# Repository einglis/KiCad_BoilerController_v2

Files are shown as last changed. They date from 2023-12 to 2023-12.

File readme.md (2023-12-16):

# Boiler Controller mk2

A whole new controller retaining the original features:

* Delayed closing valves
* Support for 24vac Nest thermostat (early US model)

And several new features:

* Multiple heating channels (zoned heating)
* ESP8266 for control and scheduling
* Greater flexibility in stat to valve mappings

The main MCU is an ESP8266 running https://github.com/einglis/SimpleNode/tree/main/examples/heating (still a WIP at the time of writing)

The valve controller is an Arduino Nano running https://github.com/einglis/boiler_valves

## HW versions

The first main board (control) had lots of drill holes that were too small; its replacement addesssed this and tidied up a few little details.

The first MCU board had pads that were too tiny to practically solder the transistors; its replacement added bigger pads, deleted the on-board status LEDs (since the MCUs have thier own), and simplified the ctrl+stat selector for the Hot Water valve.

Both replacements fixed an embarassing error where I hadn't read the ordering instructions, leaving a "Order Number Here" label present on both boards  ...along with the actual order numbers.

## v2.1 Pictures
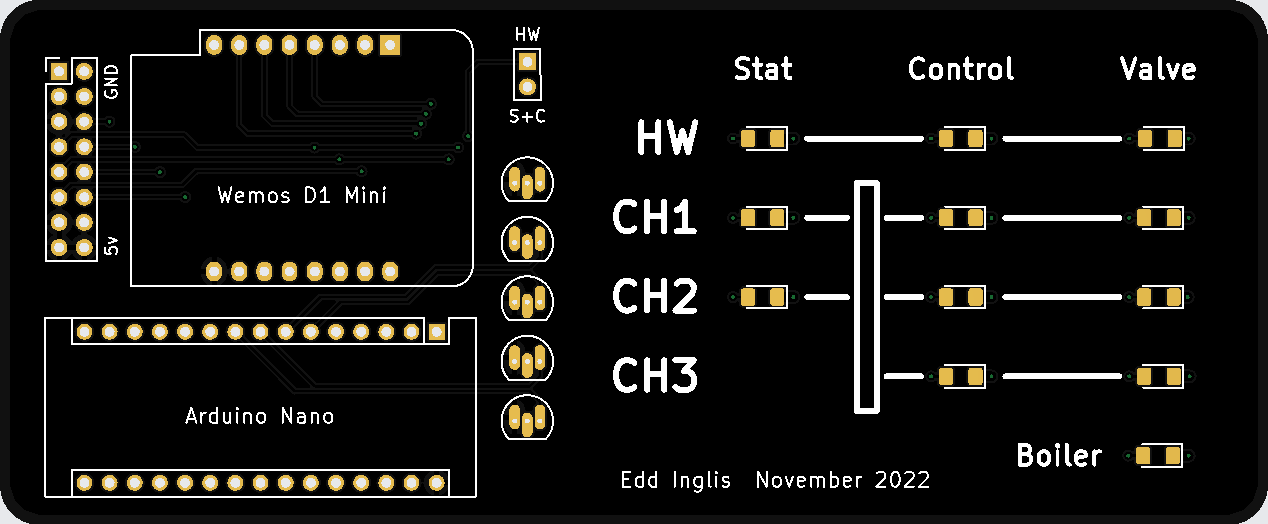
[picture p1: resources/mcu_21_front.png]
mcu_21_front

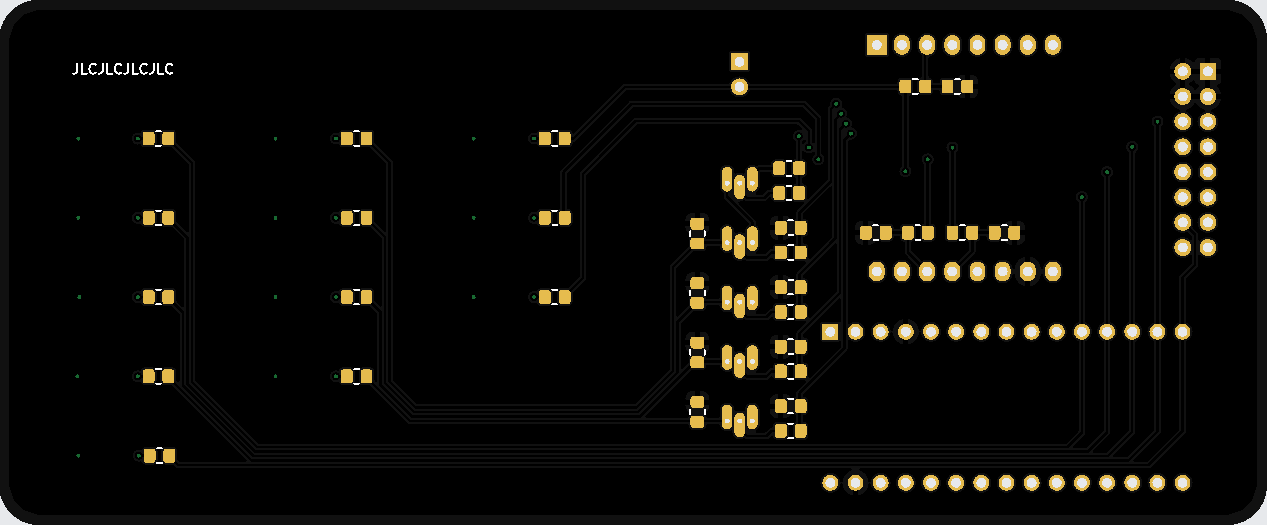
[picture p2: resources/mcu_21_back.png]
mcu_21_back

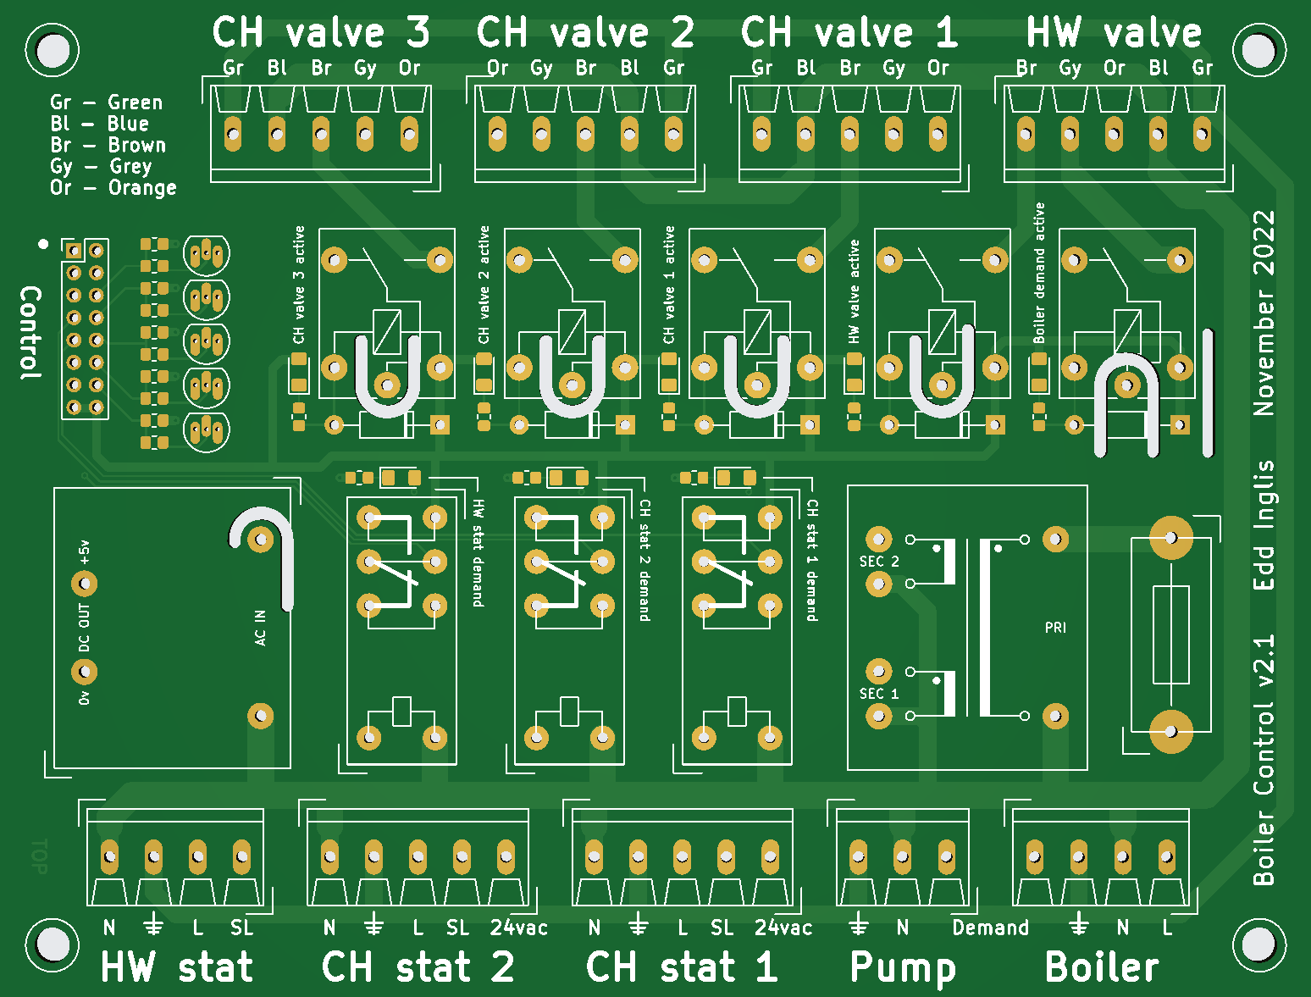
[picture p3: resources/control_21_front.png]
control_21_front

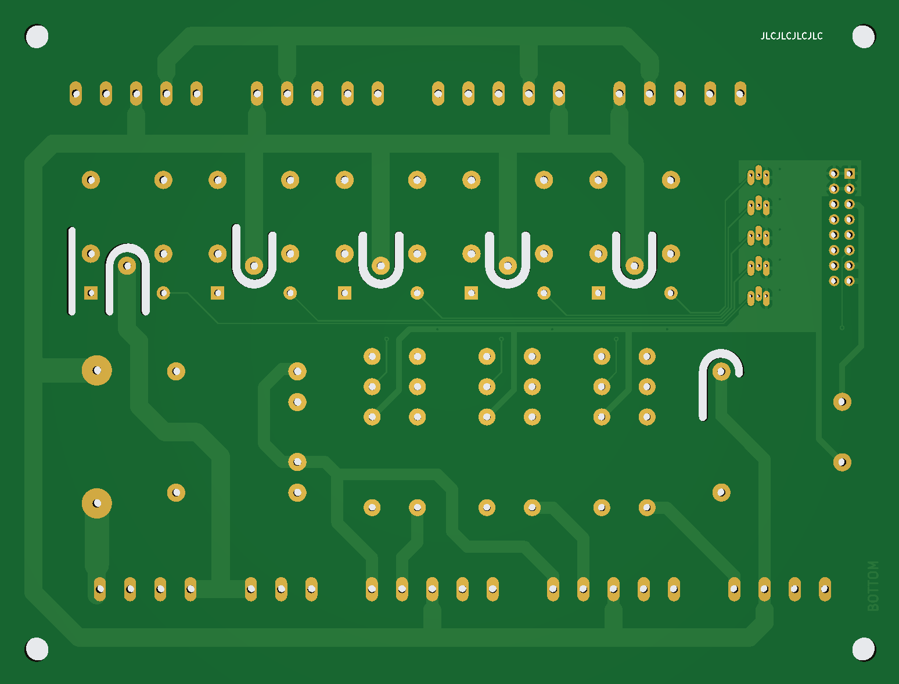
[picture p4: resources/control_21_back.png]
control_21_front


## v2.0 Pictures
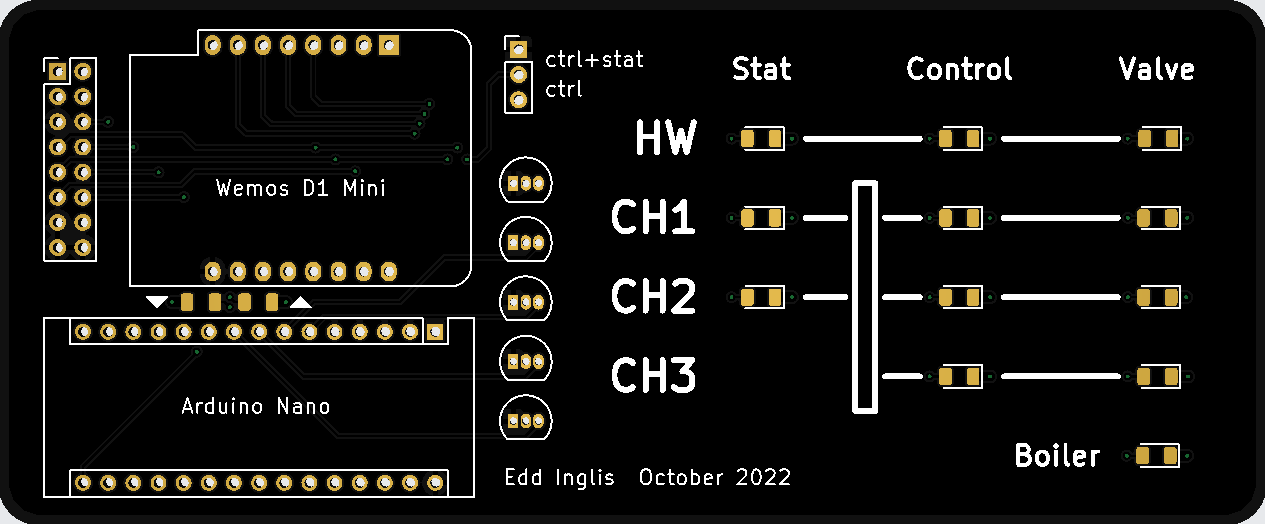
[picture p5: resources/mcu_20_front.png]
mcu_20_front

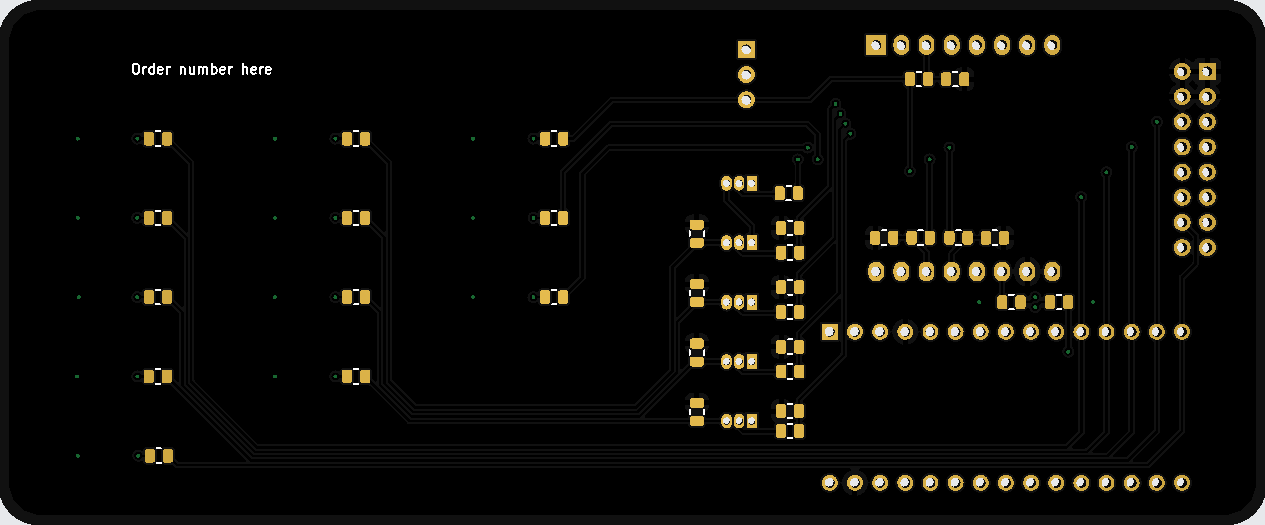
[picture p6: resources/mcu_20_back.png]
mcu_20_back

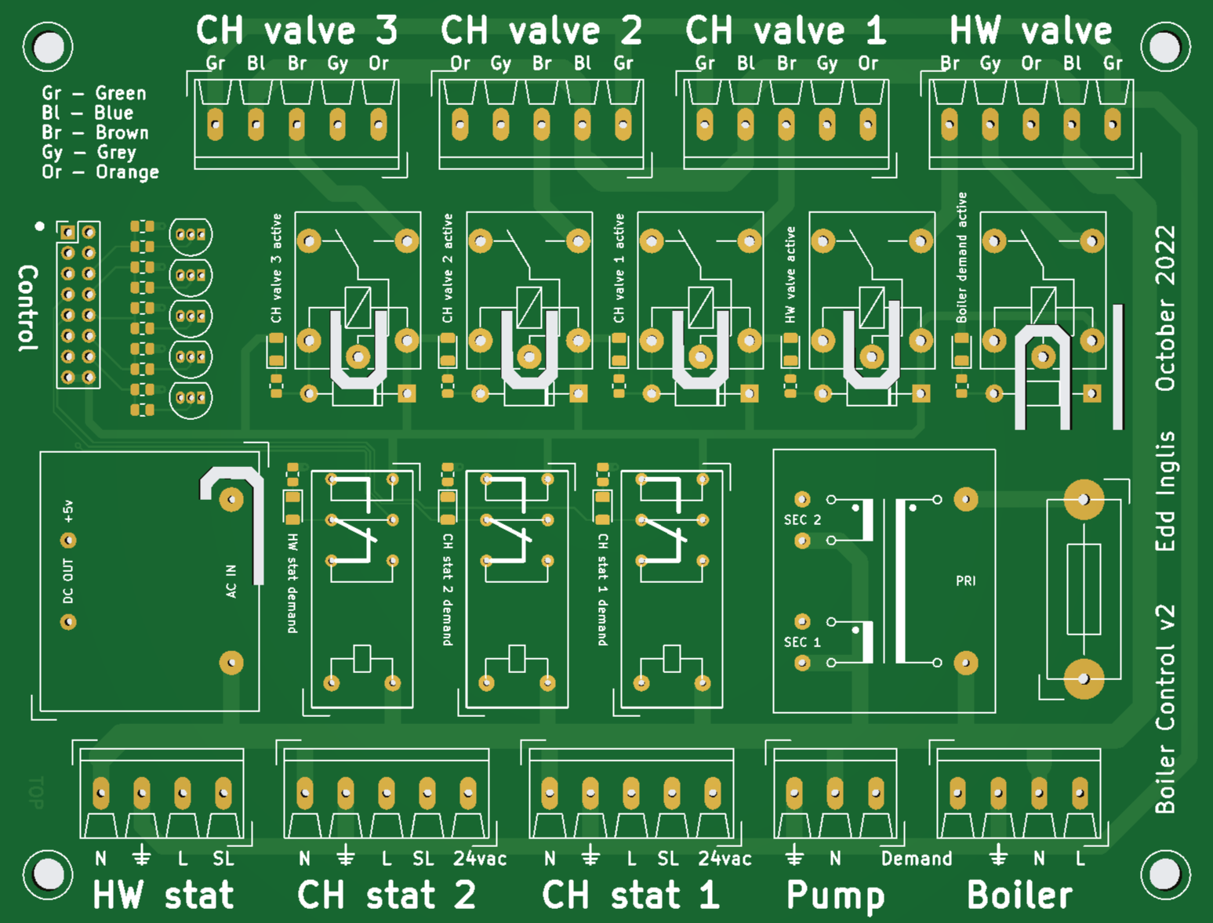
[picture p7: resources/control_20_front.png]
control_20_front

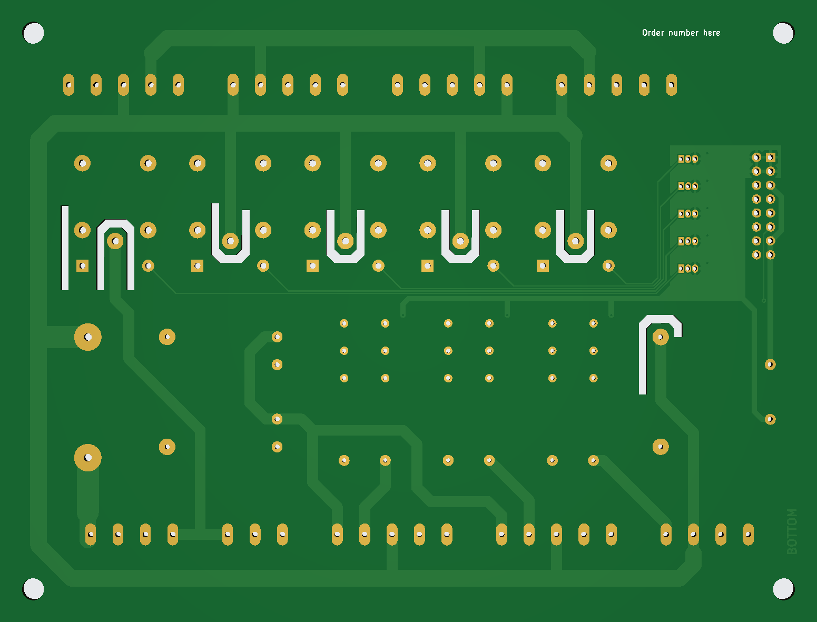
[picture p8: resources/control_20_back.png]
control_20_front


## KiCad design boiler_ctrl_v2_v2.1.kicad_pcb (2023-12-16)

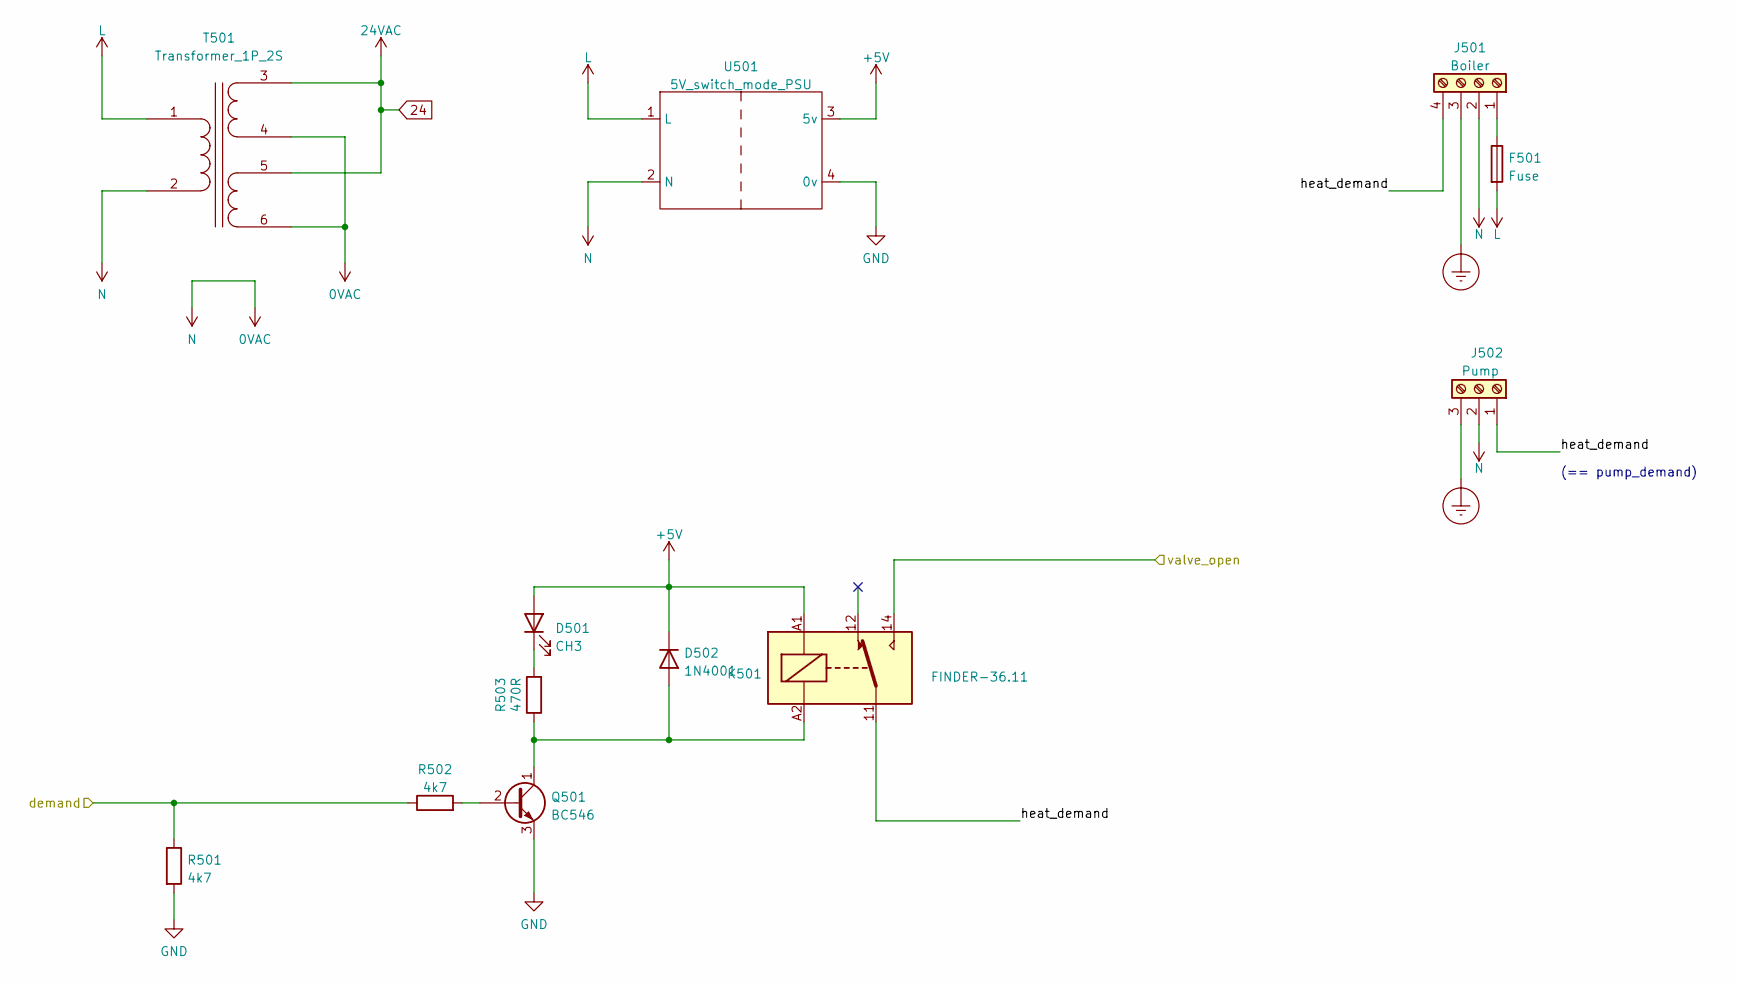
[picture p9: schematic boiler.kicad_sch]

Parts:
D501: CH3; LED_1206_3216Metric_Pad1.42x1.75mm_HandSolder
D502: 1N4001; D_DO-41_SOD81_P12mm_Horizontal
F501: Fuse; MULTICORP MC000827
J501: Boiler; CAMDENBOSS CTB0700_4
J502: Pump; CAMDENBOSS CTB0700_3
K501: FINDER-36.11; Relay_SPDT_Finder_36.11
Q501: BC546; TO-92_Inline
R501, R502: 4k7; R_0805_2012Metric_Pad1.20x1.40mm_HandSolder
R503: 470R; R_0805_2012Metric_Pad1.20x1.40mm_HandSolder
T501: Transformer_1P_2S; BLOCK VB_2.8_2_15
U501: 5V_switch_mode_PSU; MYRRA 47122

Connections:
0VAC: J501.2, J502.2, T501.2 (AB), T501.4 (SB), T501.6 (SD), U501.2 (N); also elsewhere on the board
24: T501.3 (SA), T501.5 (SC); also elsewhere on the board
/Boiler etc/heat_demand: J501.4, J502.1, K501.11
/Boiler etc/valve_open: K501.14; also elsewhere on the board
/boiler_demand: R501.1, R502.1; also elsewhere on the board
Earth_Protective: J501.3, J502.3; also elsewhere on the board
GND: Q501.3 (E), R501.2, U501.4 (0v); also elsewhere on the board
LINE: F501.2, T501.1 (AA), U501.1 (L); also elsewhere on the board
unnamed: D501.1 (K), R503.2
unnamed: D502.2 (A), K501.A2, Q501.1 (C), R503.1
unnamed: F501.1, J501.1
unnamed: Q501.2 (B), R502.2

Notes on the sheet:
(== pump_demand)

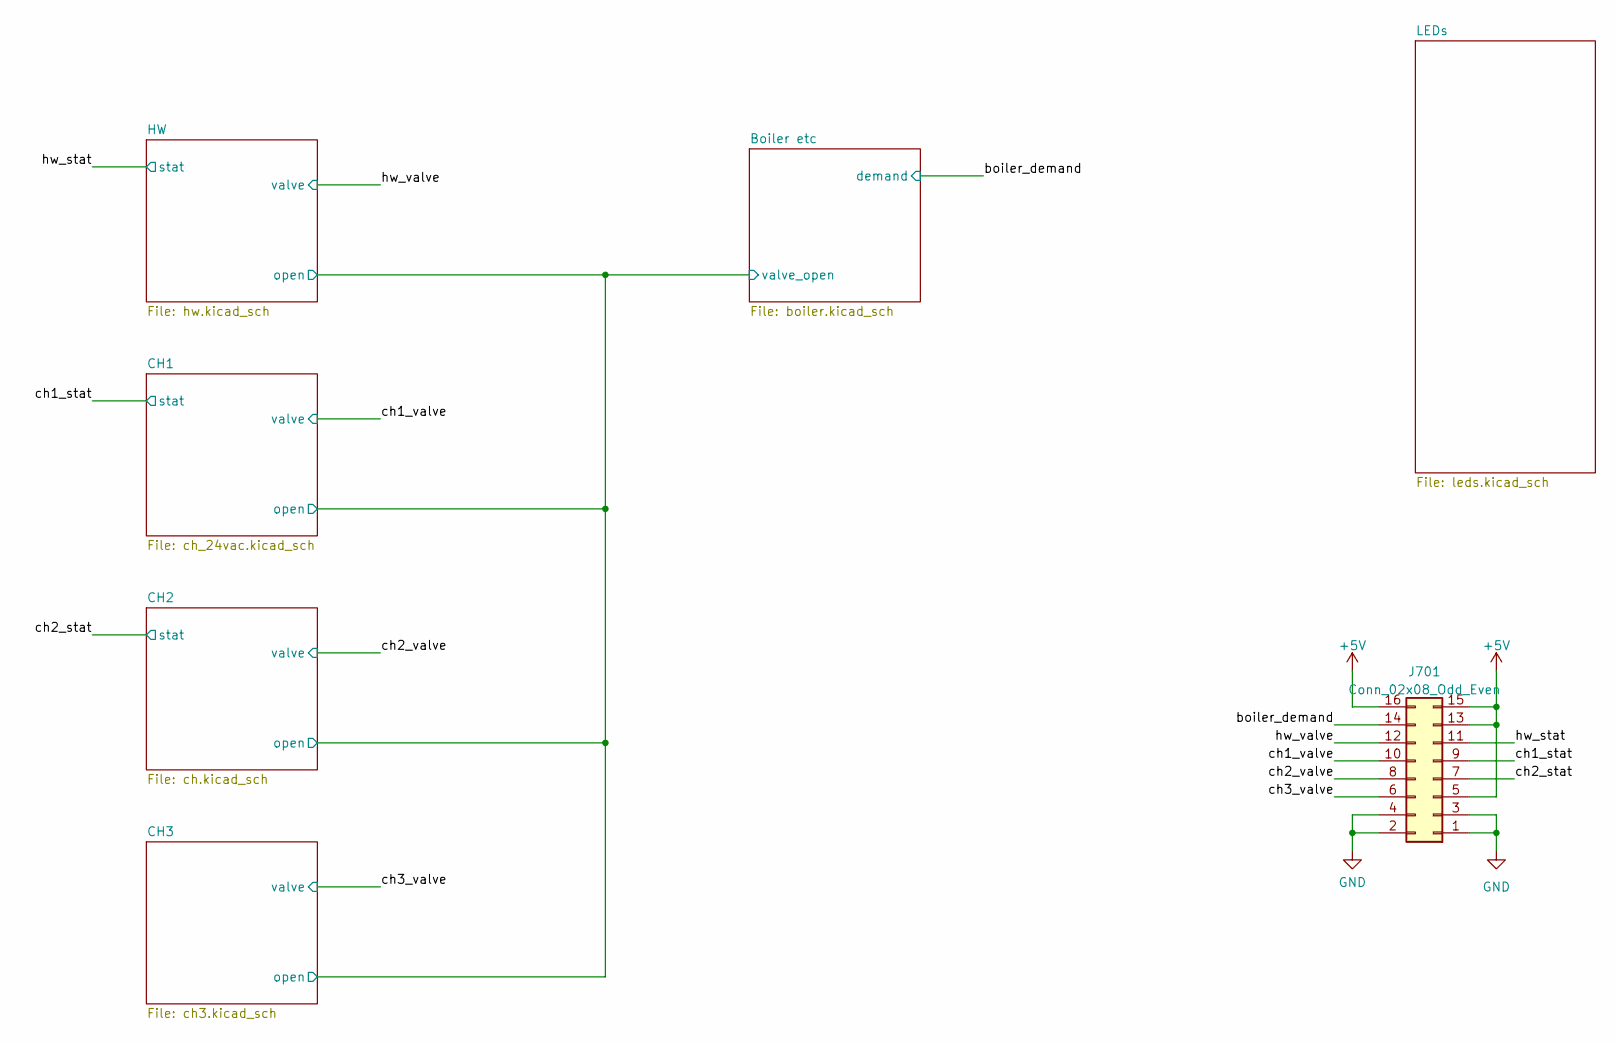
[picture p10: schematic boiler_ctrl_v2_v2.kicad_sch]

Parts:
J701: Conn_02x08_Odd_Even; PinHeader_2x08_P2.54mm_Vertical

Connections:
/boiler_demand: J701.14; also elsewhere on the board
/ch1_stat: J701.9; also elsewhere on the board
/ch1_valve: J701.10; also elsewhere on the board
/ch2_stat: J701.7; also elsewhere on the board
/ch2_valve: J701.8; also elsewhere on the board
/ch3_valve: J701.6; also elsewhere on the board
/hw_stat: J701.11; also elsewhere on the board
/hw_valve: J701.12; also elsewhere on the board
GND: J701.1, J701.2, J701.3, J701.4; also elsewhere on the board

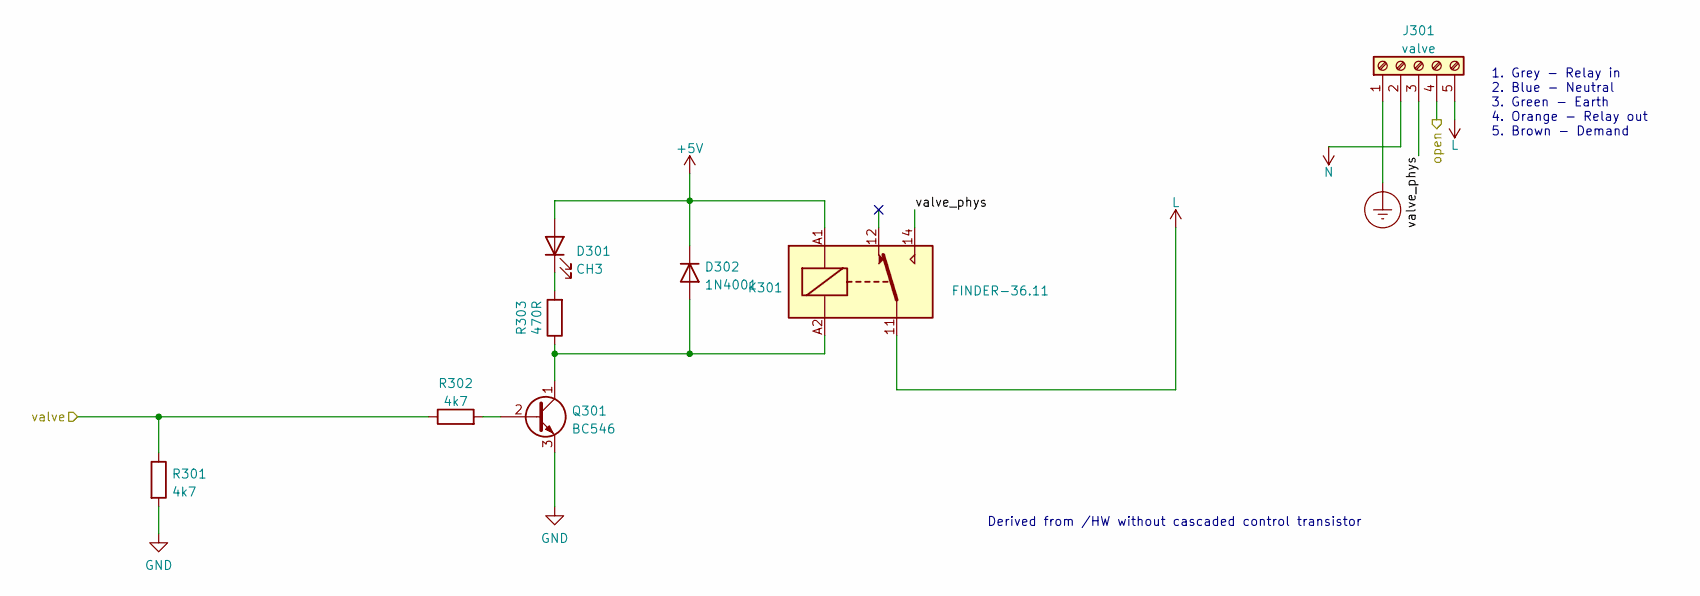
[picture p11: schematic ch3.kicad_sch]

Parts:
D301: CH3; LED_1206_3216Metric_Pad1.42x1.75mm_HandSolder
D302: 1N4001; D_DO-41_SOD81_P12mm_Horizontal
J301: valve; CAMDENBOSS CTB0700_5
K301: FINDER-36.11; Relay_SPDT_Finder_36.11
Q301: BC546; TO-92_Inline
R301, R302: 4k7; R_0805_2012Metric_Pad1.20x1.40mm_HandSolder
R303: 470R; R_0805_2012Metric_Pad1.20x1.40mm_HandSolder

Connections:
0VAC: J301.2; also elsewhere on the board
/Boiler etc/valve_open: J301.4; also elsewhere on the board
/CH3/valve_phys: J301.3, K301.14
/ch3_valve: R301.1, R302.1; also elsewhere on the board
Earth_Protective: J301.1; also elsewhere on the board
GND: Q301.3 (E), R301.2; also elsewhere on the board
LINE: J301.5, K301.11; also elsewhere on the board
unnamed: D301.1 (K), R303.2
unnamed: D302.2 (A), K301.A2, Q301.1 (C), R303.1
unnamed: Q301.2 (B), R302.2

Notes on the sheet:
Derived from /HW without cascaded control transistor
1. Grey - Relay in 2. Blue - Neutral 3. Green - Earth 4. Orange - Relay out 5. Brown - Demand

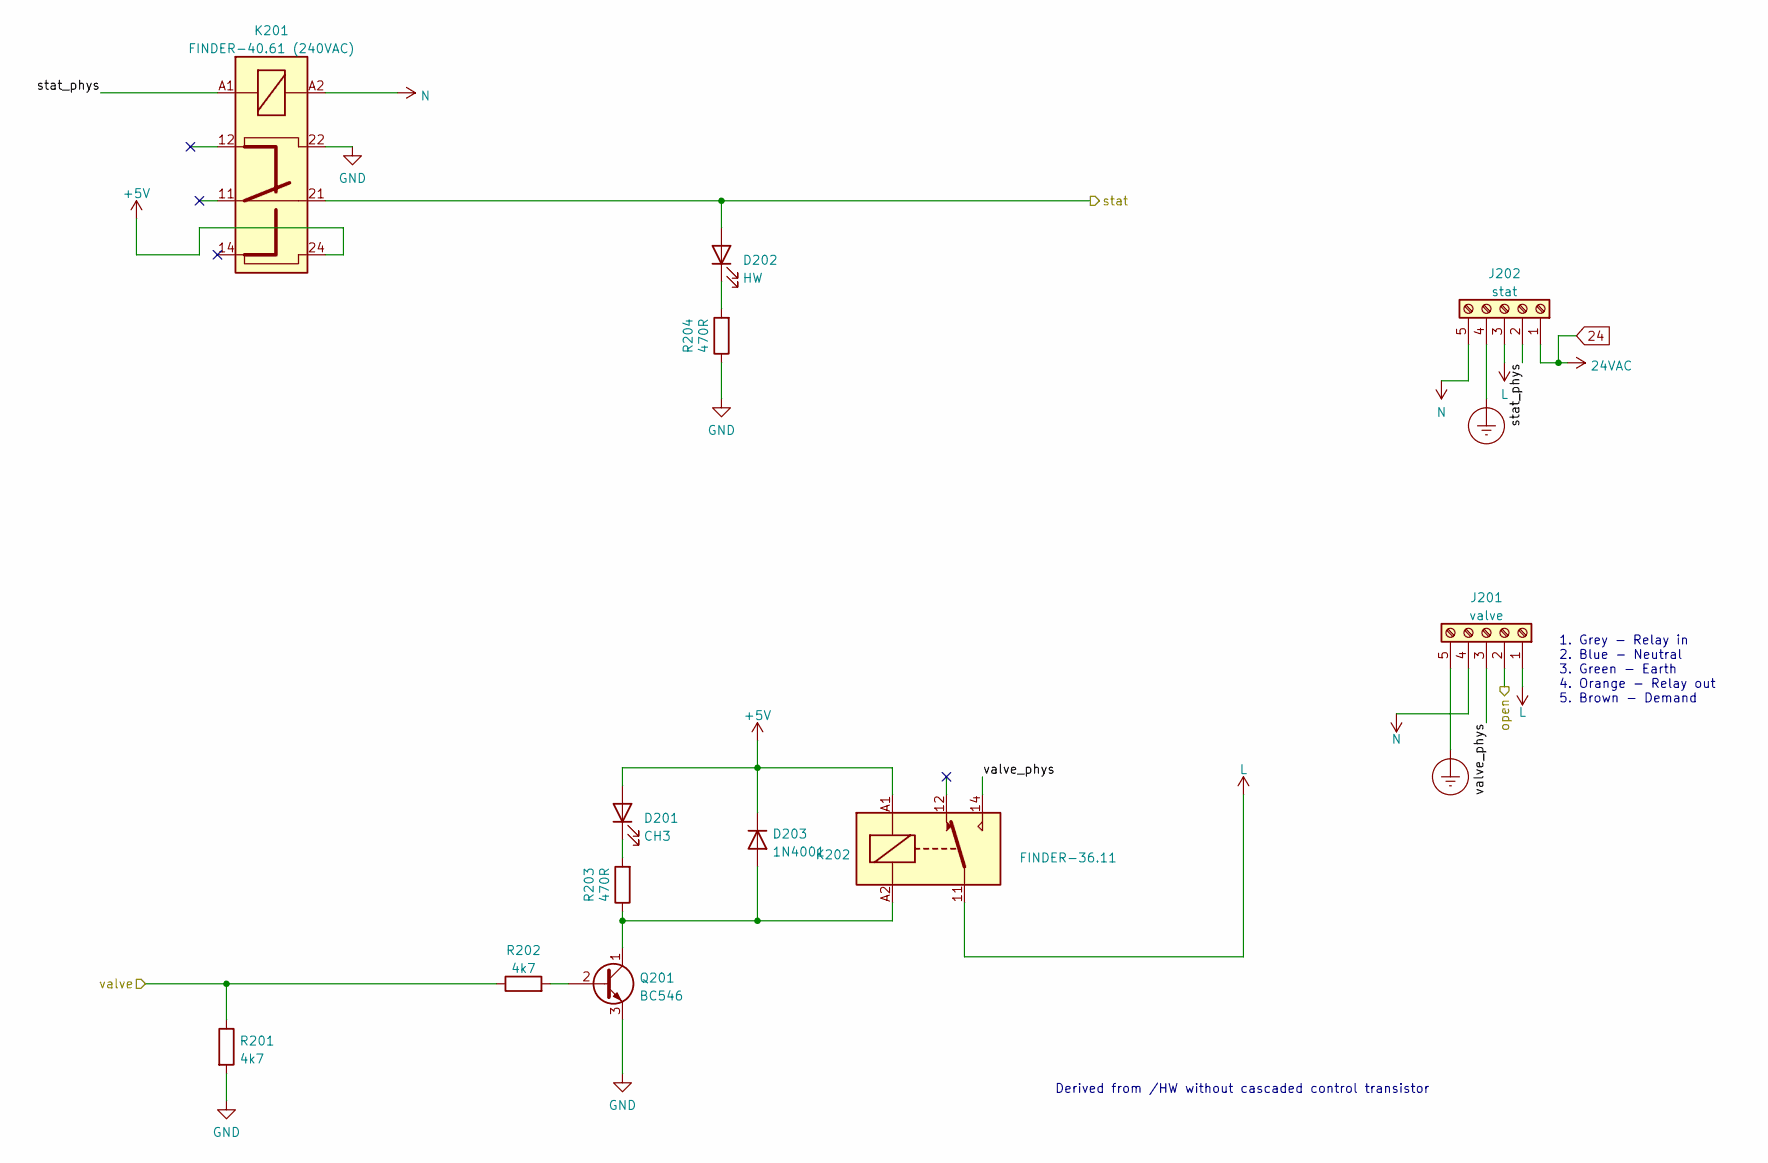
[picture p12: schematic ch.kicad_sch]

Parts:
D201: CH3; LED_1206_3216Metric_Pad1.42x1.75mm_HandSolder
D202: HW; LED_1206_3216Metric_Pad1.42x1.75mm_HandSolder
D203: 1N4001; D_DO-41_SOD81_P12mm_Horizontal
J201: valve; CAMDENBOSS CTB0700_5
J202: stat; CAMDENBOSS CTB0700_5
K201: FINDER-40.61 (240VAC); FINDER 40.61
K202: FINDER-36.11; Relay_SPDT_Finder_36.11
Q201: BC546; TO-92_Inline
R201, R202: 4k7; R_0805_2012Metric_Pad1.20x1.40mm_HandSolder
R203, R204: 470R; R_0805_2012Metric_Pad1.20x1.40mm_HandSolder

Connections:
0VAC: J201.4, J202.5, K201.A2; also elsewhere on the board
24: J202.1; also elsewhere on the board
/Boiler etc/valve_open: J201.2; also elsewhere on the board
/CH2/stat_phys: J202.2, K201.A1
/CH2/valve_phys: J201.3, K202.14
/ch2_stat: D202.2 (A), K201.21; also elsewhere on the board
/ch2_valve: R201.1, R202.1; also elsewhere on the board
Earth_Protective: J201.5, J202.4; also elsewhere on the board
GND: K201.22, Q201.3 (E), R201.2, R204.1; also elsewhere on the board
LINE: J201.1, J202.3, K202.11; also elsewhere on the board
unnamed: D201.1 (K), R203.2
unnamed: D202.1 (K), R204.2
unnamed: D203.2 (A), K202.A2, Q201.1 (C), R203.1
unnamed: Q201.2 (B), R202.2

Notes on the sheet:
Derived from /HW without cascaded control transistor
1. Grey - Relay in 2. Blue - Neutral 3. Green - Earth 4. Orange - Relay out 5. Brown - Demand

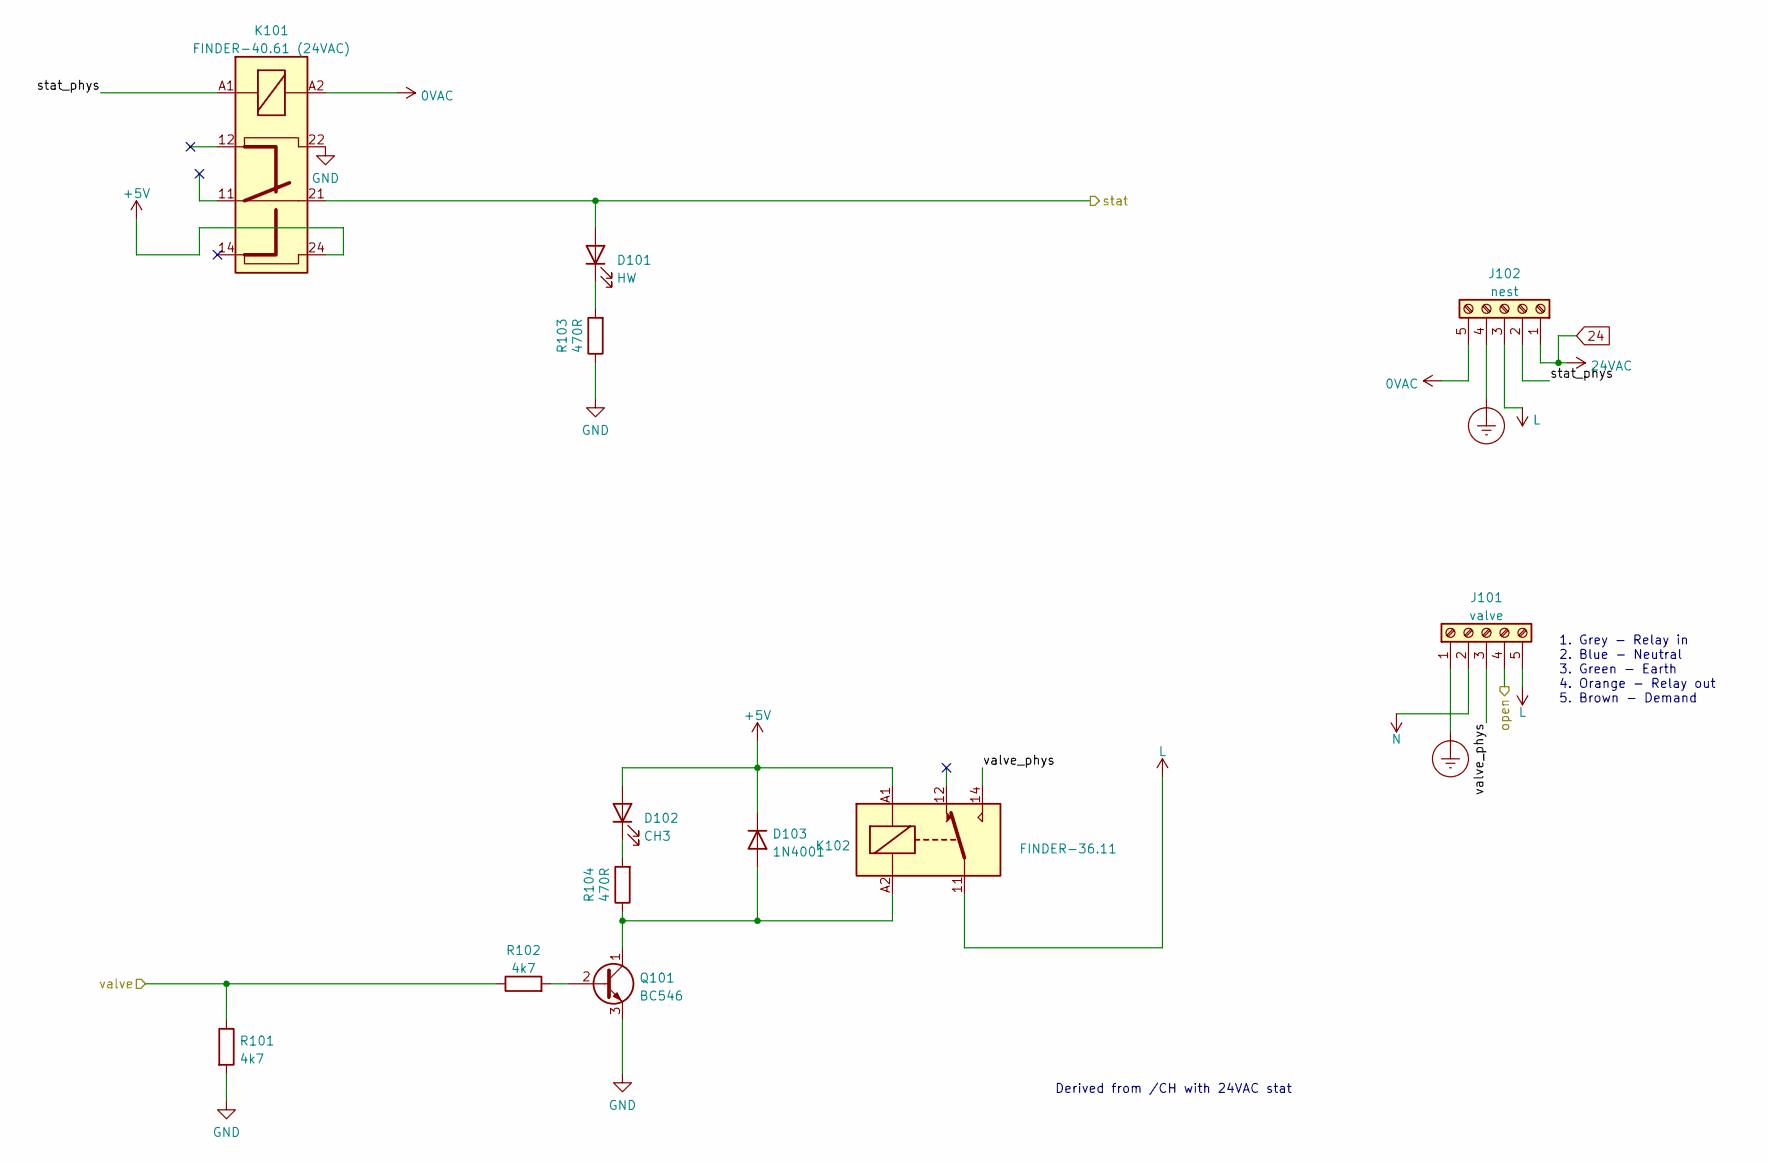
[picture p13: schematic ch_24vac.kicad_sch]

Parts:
D101: HW; LED_1206_3216Metric_Pad1.42x1.75mm_HandSolder
D102: CH3; LED_1206_3216Metric_Pad1.42x1.75mm_HandSolder
D103: 1N4001; D_DO-41_SOD81_P12mm_Horizontal
J101: valve; CAMDENBOSS CTB0700_5
J102: nest; CAMDENBOSS CTB0700_5
K101: FINDER-40.61 (24VAC); FINDER 40.61
K102: FINDER-36.11; Relay_SPDT_Finder_36.11
Q101: BC546; TO-92_Inline
R101, R102: 4k7; R_0805_2012Metric_Pad1.20x1.40mm_HandSolder
R103, R104: 470R; R_0805_2012Metric_Pad1.20x1.40mm_HandSolder

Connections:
0VAC: J101.2, J102.5, K101.A2; also elsewhere on the board
24: J102.1; also elsewhere on the board
/Boiler etc/valve_open: J101.4; also elsewhere on the board
/CH1/stat_phys: J102.2, K101.A1
/CH1/valve_phys: J101.3, K102.14
/ch1_stat: D101.2 (A), K101.21; also elsewhere on the board
/ch1_valve: R101.1, R102.1; also elsewhere on the board
Earth_Protective: J101.1, J102.4; also elsewhere on the board
GND: K101.22, Q101.3 (E), R101.2, R103.1; also elsewhere on the board
LINE: J101.5, J102.3, K102.11; also elsewhere on the board
unnamed: D101.1 (K), R103.2
unnamed: D102.1 (K), R104.2
unnamed: D103.2 (A), K102.A2, Q101.1 (C), R104.1
unnamed: Q101.2 (B), R102.2

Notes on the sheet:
Derived from /CH with 24VAC stat
1. Grey - Relay in 2. Blue - Neutral 3. Green - Earth 4. Orange - Relay out 5. Brown - Demand

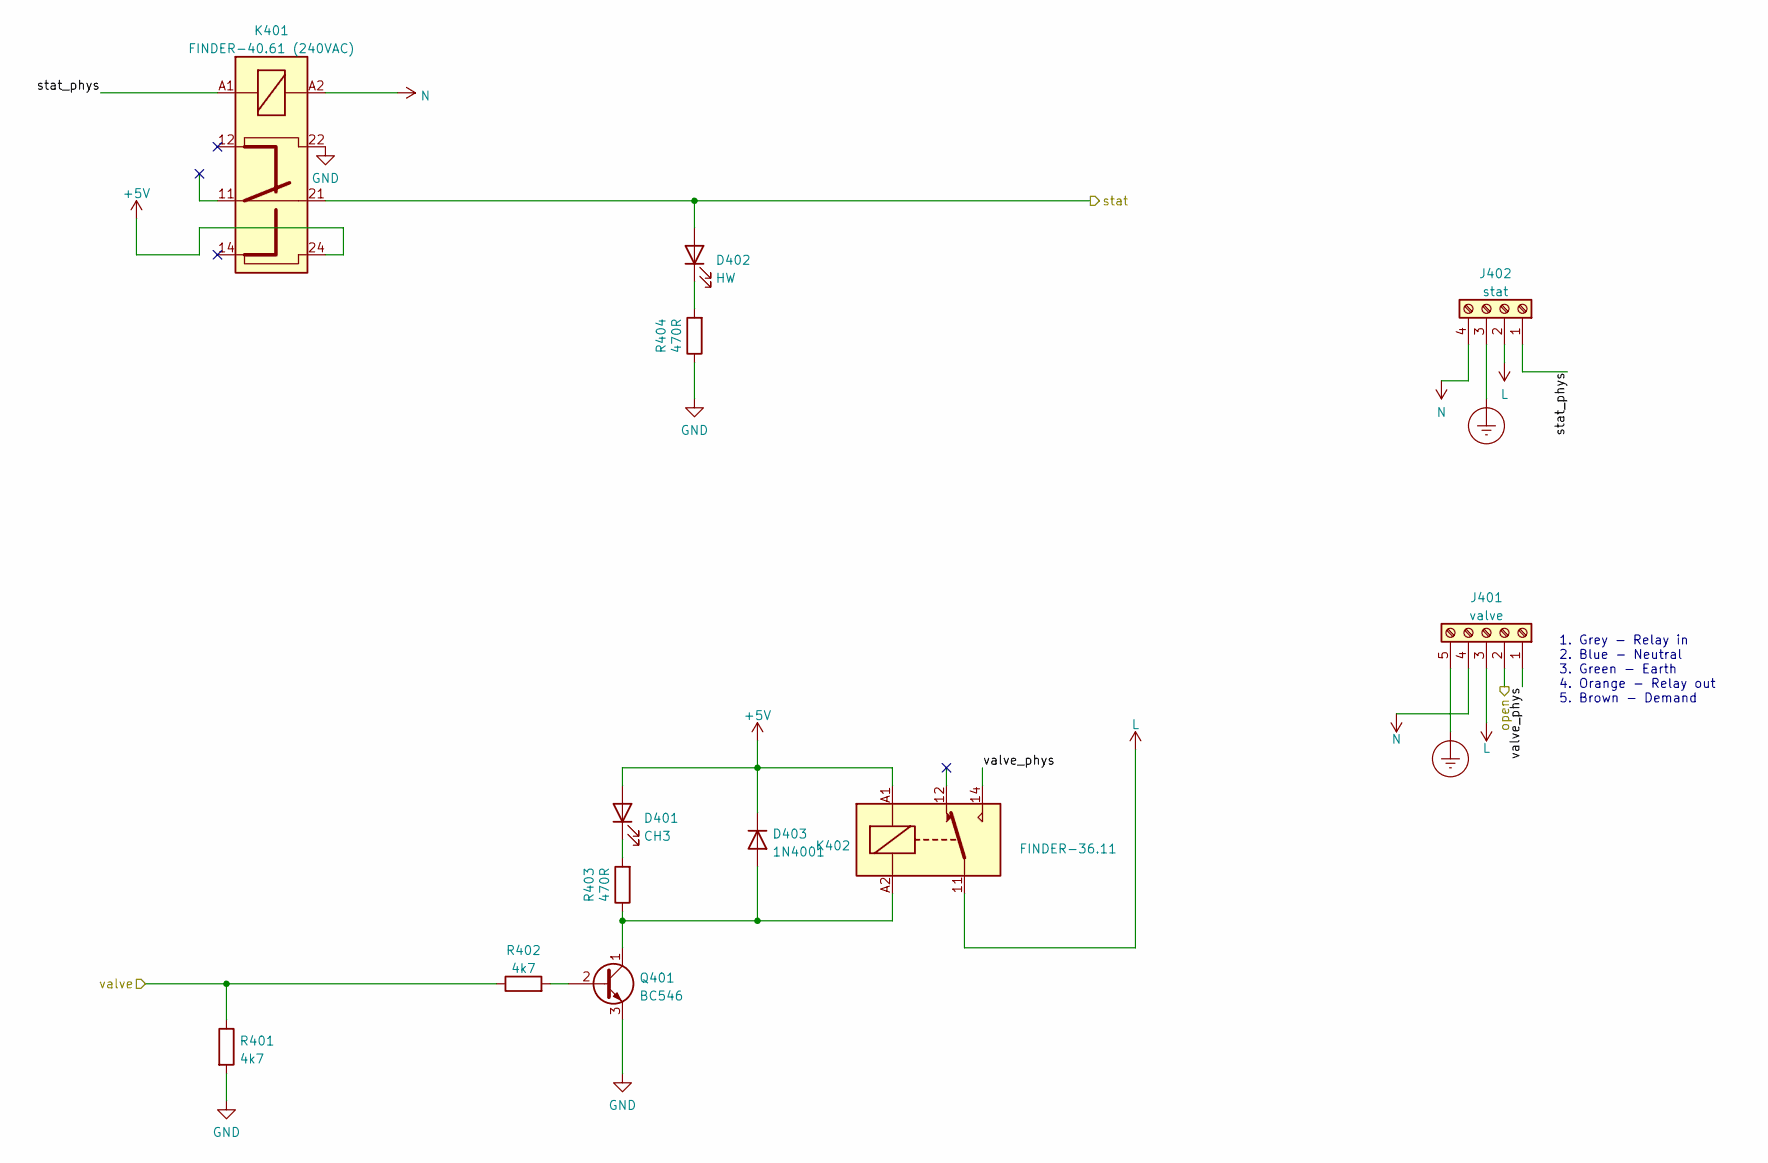
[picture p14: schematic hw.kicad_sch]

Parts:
D401: CH3; LED_1206_3216Metric_Pad1.42x1.75mm_HandSolder
D402: HW; LED_1206_3216Metric_Pad1.42x1.75mm_HandSolder
D403: 1N4001; D_DO-41_SOD81_P12mm_Horizontal
J401: valve; CAMDENBOSS CTB0700_5
J402: stat; CAMDENBOSS CTB0700_4
K401: FINDER-40.61 (240VAC); FINDER 40.61
K402: FINDER-36.11; Relay_SPDT_Finder_36.11
Q401: BC546; TO-92_Inline
R401, R402: 4k7; R_0805_2012Metric_Pad1.20x1.40mm_HandSolder
R403, R404: 470R; R_0805_2012Metric_Pad1.20x1.40mm_HandSolder

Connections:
0VAC: J401.4, J402.4, K401.A2; also elsewhere on the board
/Boiler etc/valve_open: J401.2; also elsewhere on the board
/HW/stat_phys: J402.1, K401.A1
/HW/valve_phys: J401.1, K402.14
/hw_stat: D402.2 (A), K401.21; also elsewhere on the board
/hw_valve: R401.1, R402.1; also elsewhere on the board
Earth_Protective: J401.5, J402.3; also elsewhere on the board
GND: K401.22, Q401.3 (E), R401.2, R404.1; also elsewhere on the board
LINE: J401.3, J402.2, K402.11; also elsewhere on the board
unnamed: D401.1 (K), R403.2
unnamed: D402.1 (K), R404.2
unnamed: D403.2 (A), K402.A2, Q401.1 (C), R403.1
unnamed: Q401.2 (B), R402.2

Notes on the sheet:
1. Grey - Relay in 2. Blue - Neutral 3. Green - Earth 4. Orange - Relay out 5. Brown - Demand

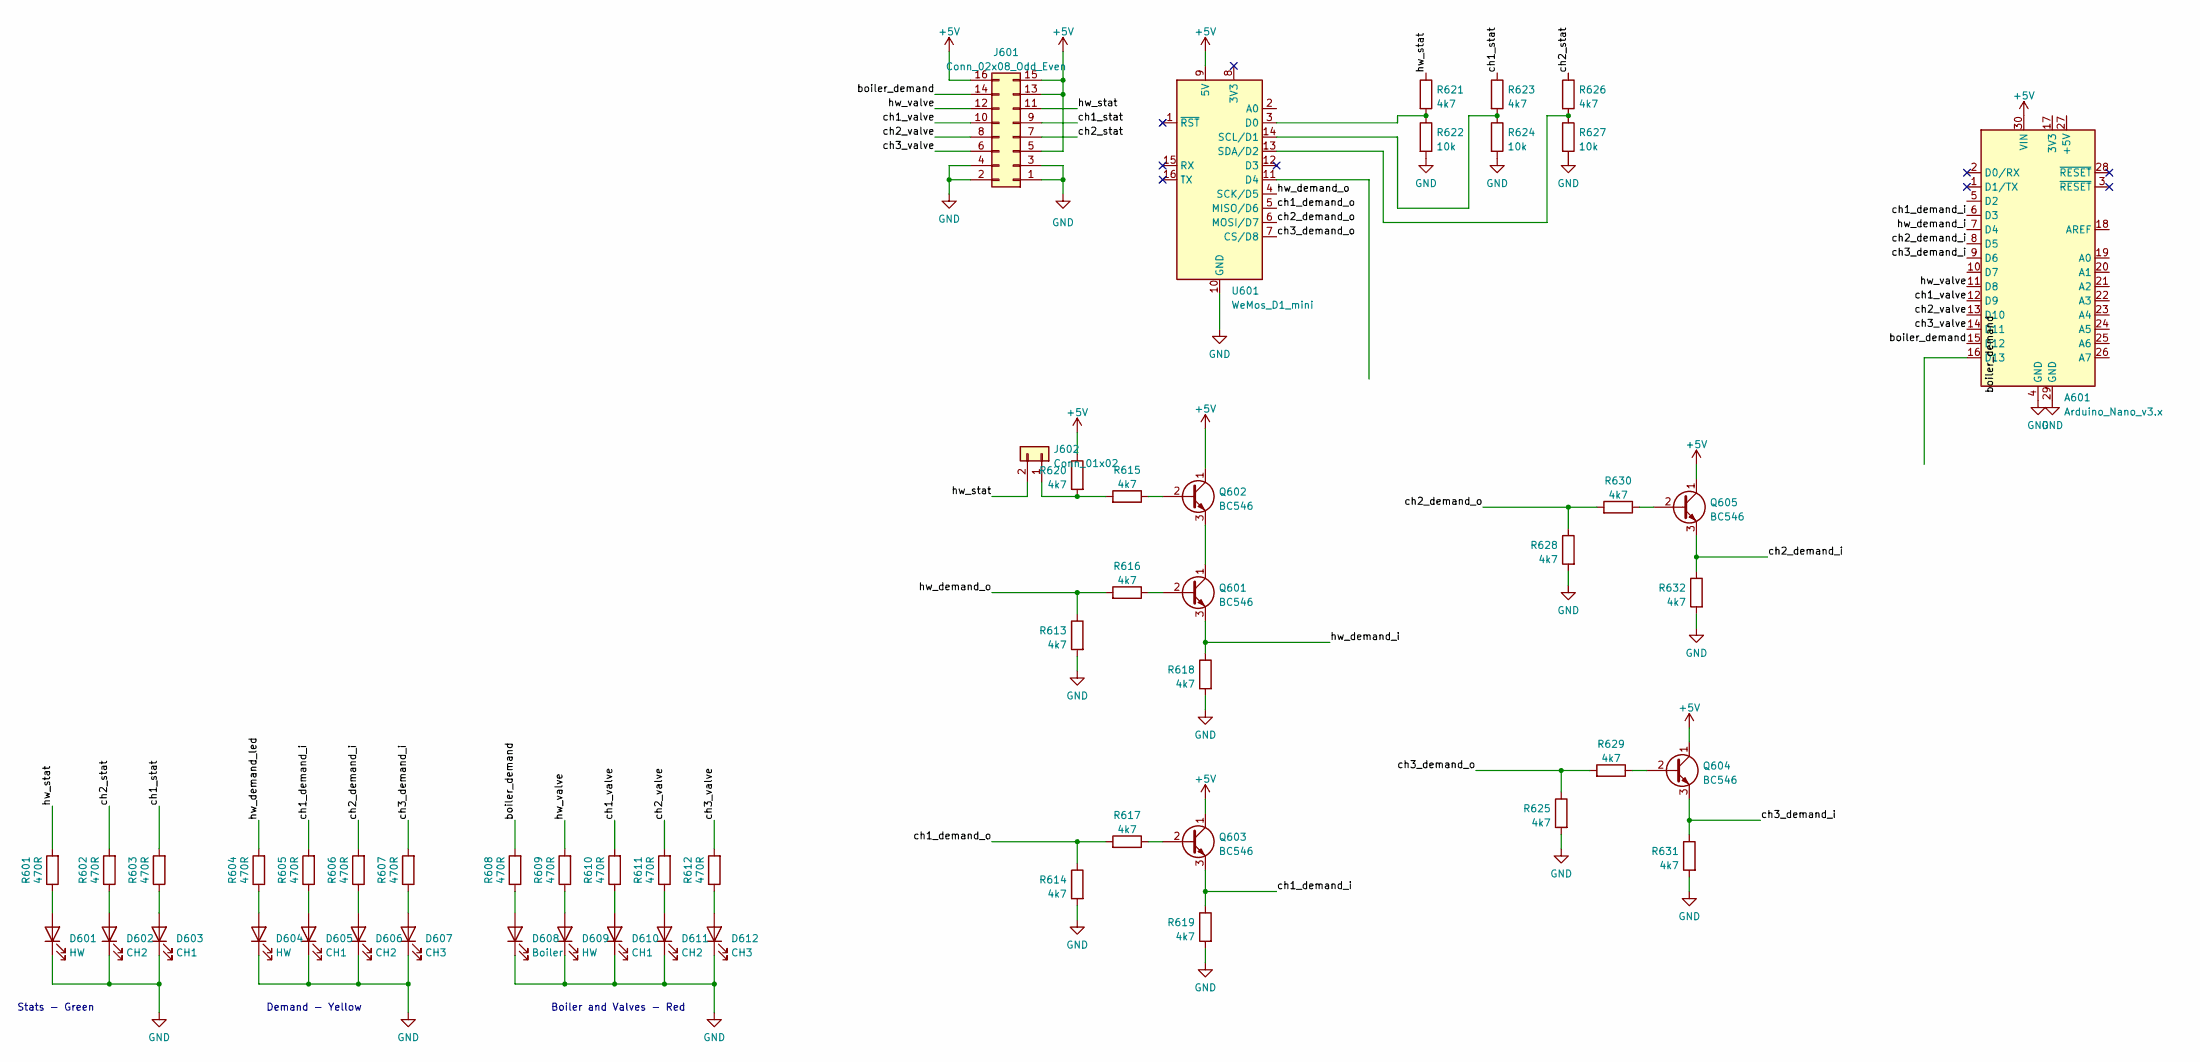
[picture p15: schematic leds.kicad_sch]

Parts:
A601: Arduino_Nano_v3.x; Arduino_Nano
D601, D604, D609: HW; LED_1206_3216Metric_Pad1.42x1.75mm_HandSolder
D602, D606, D611: CH2; LED_1206_3216Metric_Pad1.42x1.75mm_HandSolder
D603, D605, D610: CH1; LED_1206_3216Metric_Pad1.42x1.75mm_HandSolder
D607, D612: CH3; LED_1206_3216Metric_Pad1.42x1.75mm_HandSolder
D608: Boiler; LED_1206_3216Metric_Pad1.42x1.75mm_HandSolder
J601: Conn_02x08_Odd_Even; PinHeader_2x08_P2.54mm_Vertical
J602: Conn_01x02; PinHeader_1x02_P2.54mm_Vertical
Q601, Q602, Q603, Q604, Q605: BC546; TO-92_Inline
R601, R602, R603, R604, R605, R606, R607, R608, R609, R610, R611, R612: 470R; R_0805_2012Metric_Pad1.20x1.40mm_HandSolder
R613, R614, R615, R616, R617, R618, R619, R620, R621, R623, R625, R626, R628, R629, R630, R631, R632: 4k7; R_0805_2012Metric_Pad1.20x1.40mm_HandSolder
R622, R624, R627: 10k; R_0805_2012Metric_Pad1.20x1.40mm_HandSolder
U601: WeMos_D1_mini; WEMOS_D1_mini_light

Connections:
/LEDs/boiler_demand: A601.15 (D12), J601.14, R608.2
/LEDs/ch1_demand_i: A601.6 (D3), Q603.3 (E), R605.2, R619.1
/LEDs/ch1_demand_o: R614.1, R617.2, U601.5 (MISO/D6)
/LEDs/ch1_stat: J601.9, R603.2, R623.1
/LEDs/ch1_valve: A601.12 (D9), J601.10, R610.2
/LEDs/ch2_demand_i: A601.8 (D5), Q605.3 (E), R606.2, R632.1
/LEDs/ch2_demand_o: R628.1, R630.2, U601.6 (MOSI/D7)
/LEDs/ch2_stat: J601.7, R602.2, R626.1
/LEDs/ch2_valve: A601.13 (D10), J601.8, R611.2
/LEDs/ch3_demand_i: A601.9 (D6), Q604.3 (E), R607.2, R631.1
/LEDs/ch3_demand_o: R625.1, R629.2, U601.7 (CS/D8)
/LEDs/ch3_valve: A601.14 (D11), J601.6, R612.2
/LEDs/hw_demand_o: R613.1, R616.2, U601.4 (SCK/D5)
/LEDs/hw_stat: J601.11, J602.2, R601.2, R621.1
/LEDs/hw_valve: A601.11 (D8), J601.12, R609.2
GND: A601.4 (GND), A601.29 (GND), D601.1 (K), D602.1 (K), D603.1 (K), D604.1 (K), D605.1 (K), D606.1 (K), D607.1 (K), D608.1 (K), D609.1 (K), D610.1 (K), D611.1 (K), D612.1 (K), J601.1, J601.2, J601.3, J601.4, R613.2, R614.2, R618.2, R619.2, R622.2, R624.2, R625.2, R627.2, R628.2, R631.2, R632.2, U601.10 (GND); also elsewhere on the board
unnamed: D601.2 (A), R601.1
unnamed: D602.2 (A), R602.1
unnamed: D603.2 (A), R603.1
unnamed: D604.2 (A), R604.1
unnamed: D605.2 (A), R605.1
unnamed: D606.2 (A), R606.1
unnamed: D607.2 (A), R607.1
unnamed: D608.2 (A), R608.1
unnamed: D609.2 (A), R609.1
unnamed: D610.2 (A), R610.1
unnamed: D611.2 (A), R611.1
unnamed: D612.2 (A), R612.1
unnamed: Q603.2 (B), R617.1
unnamed: Q604.2 (B), R629.1
unnamed: Q605.2 (B), R630.1
unnamed: J602.1, R615.2, R620.2
unnamed: R621.2, R622.1, U601.3 (D0)
unnamed: R623.2, R624.1, U601.14 (SCL/D1)
unnamed: R626.2, R627.1, U601.13 (SDA/D2)

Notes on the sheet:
Boiler and Valves - Red
Demand - Yellow
Stats - Green

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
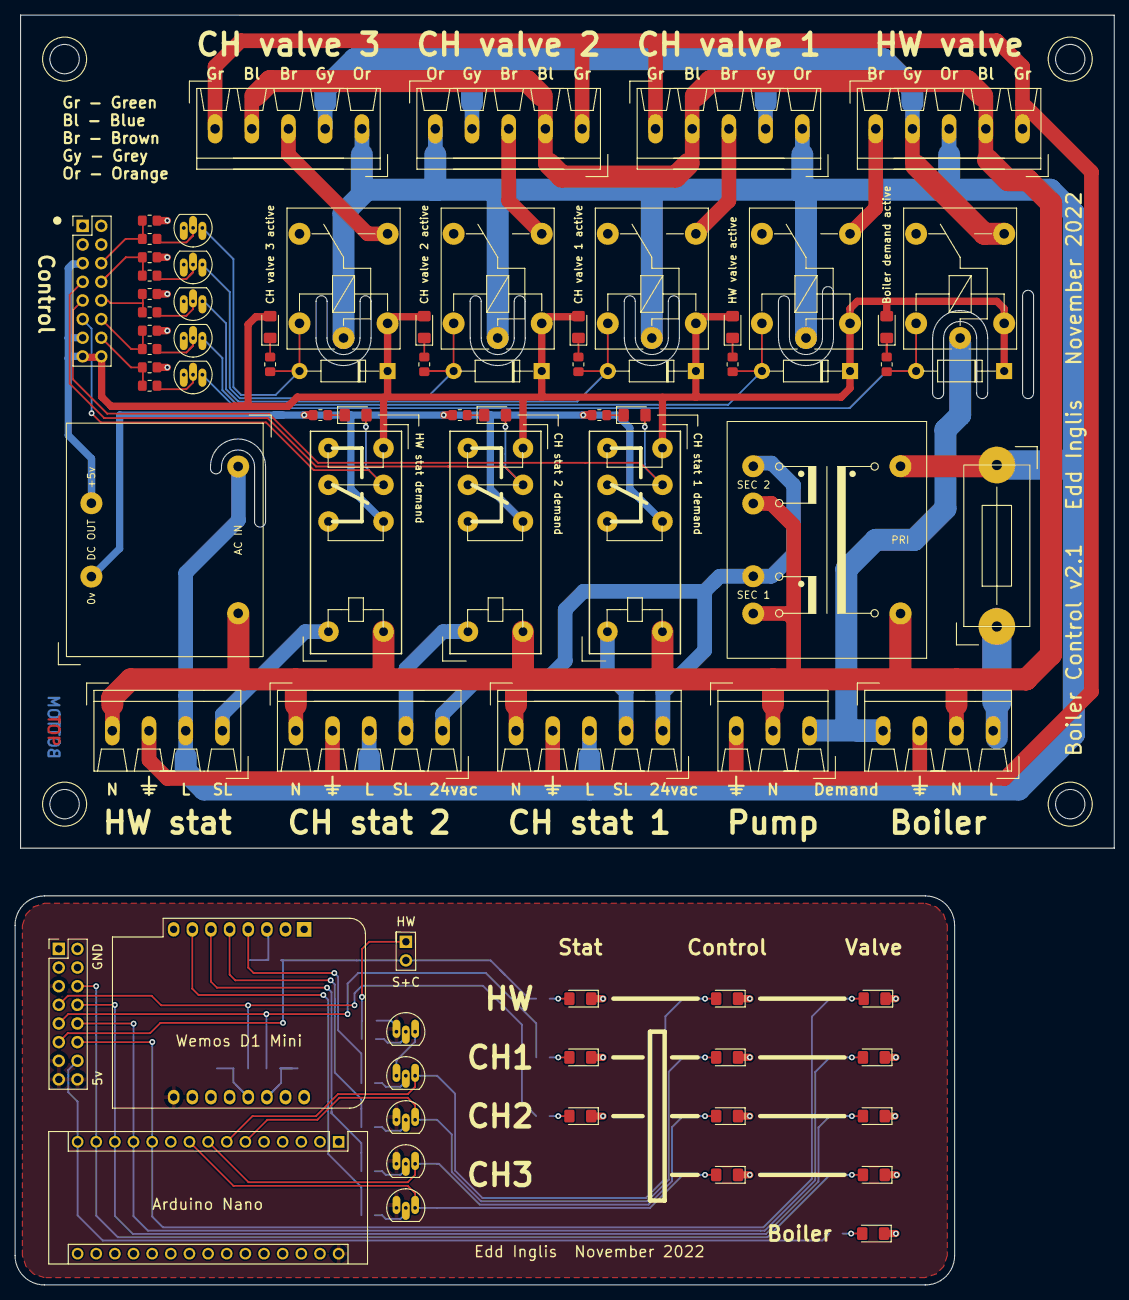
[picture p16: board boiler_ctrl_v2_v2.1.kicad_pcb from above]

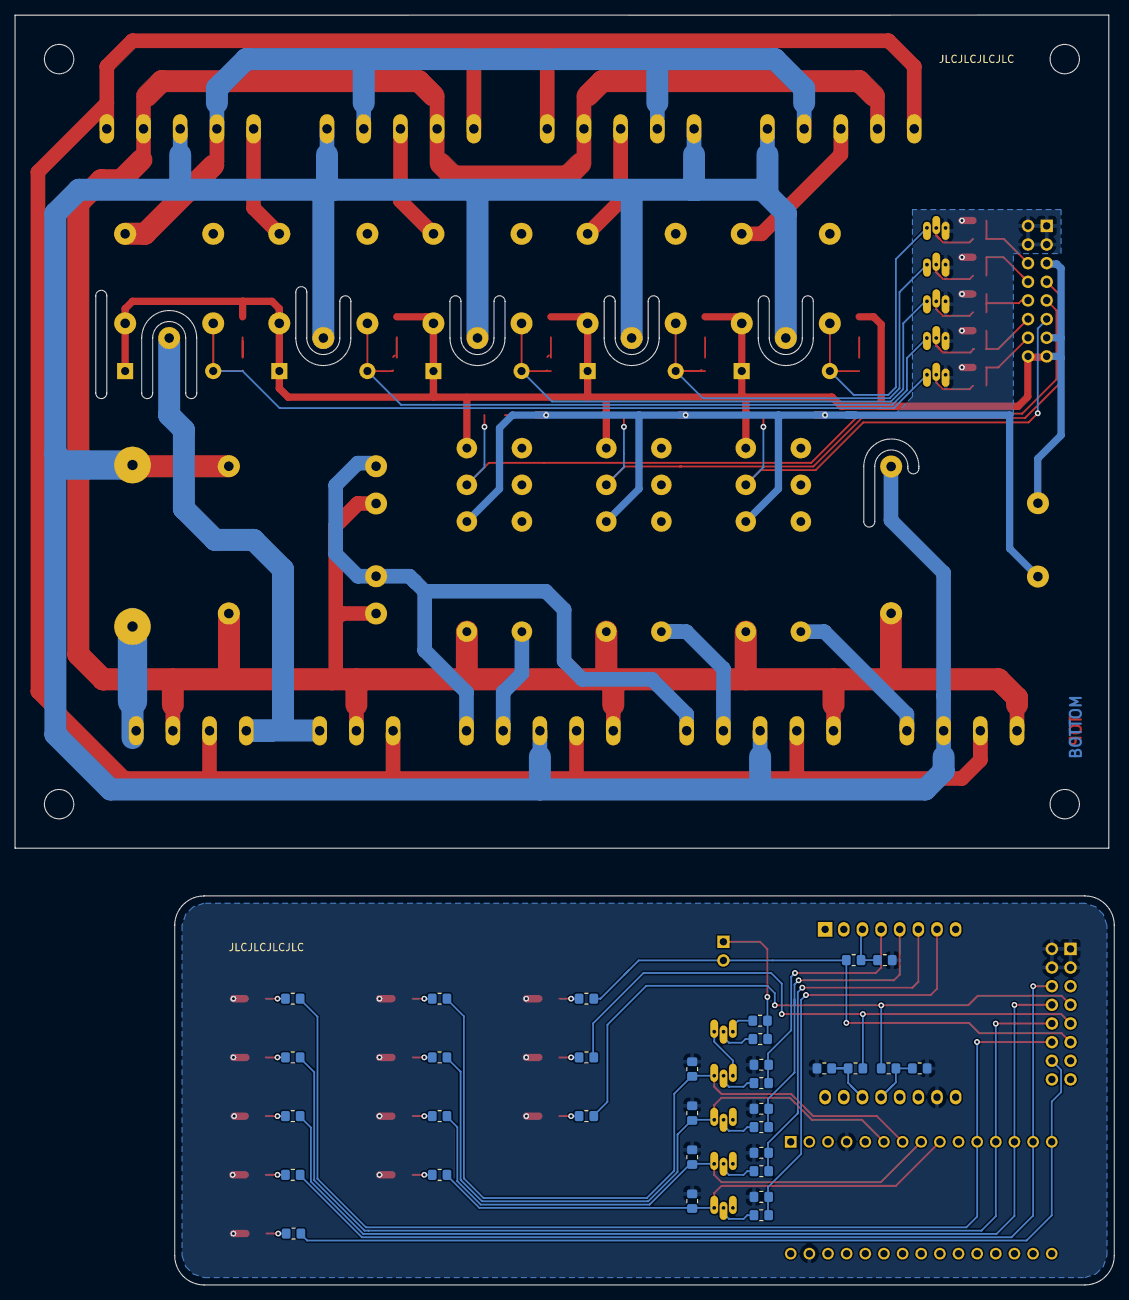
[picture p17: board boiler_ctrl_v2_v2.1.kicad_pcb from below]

Board: 4 copper layers, 149.8 x 173.0 mm, 110 parts (32 on the bottom side), 80 nets.
